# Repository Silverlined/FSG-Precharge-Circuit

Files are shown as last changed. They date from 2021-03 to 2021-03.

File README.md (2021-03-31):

# 600V Pre-charge Circuit

One of the challenges that arise in tractive systems
of electric cars is establishing a reliable connection between
the accumulator and inverter. The presented pre-charge control
circuit is a potential solution that can be used to operate a DC
contractor and prevent the flow of high inrush current into the
inverter. The circuit has been simulated in LTspice and tested
in real life across the temperature range of +10 °C to +65 °C.
Pre-charging is stopped once the inverter voltage exceeds 98%
of the voltage level of the accumulator and resumed when it is
below 95%. Regardless, this design is incomplete. There are several design flaws that have been discovered and therefore require further development.

2-layer PCB designed in EasyEDA. Gerber and assembly files are in the relevant repo folders.

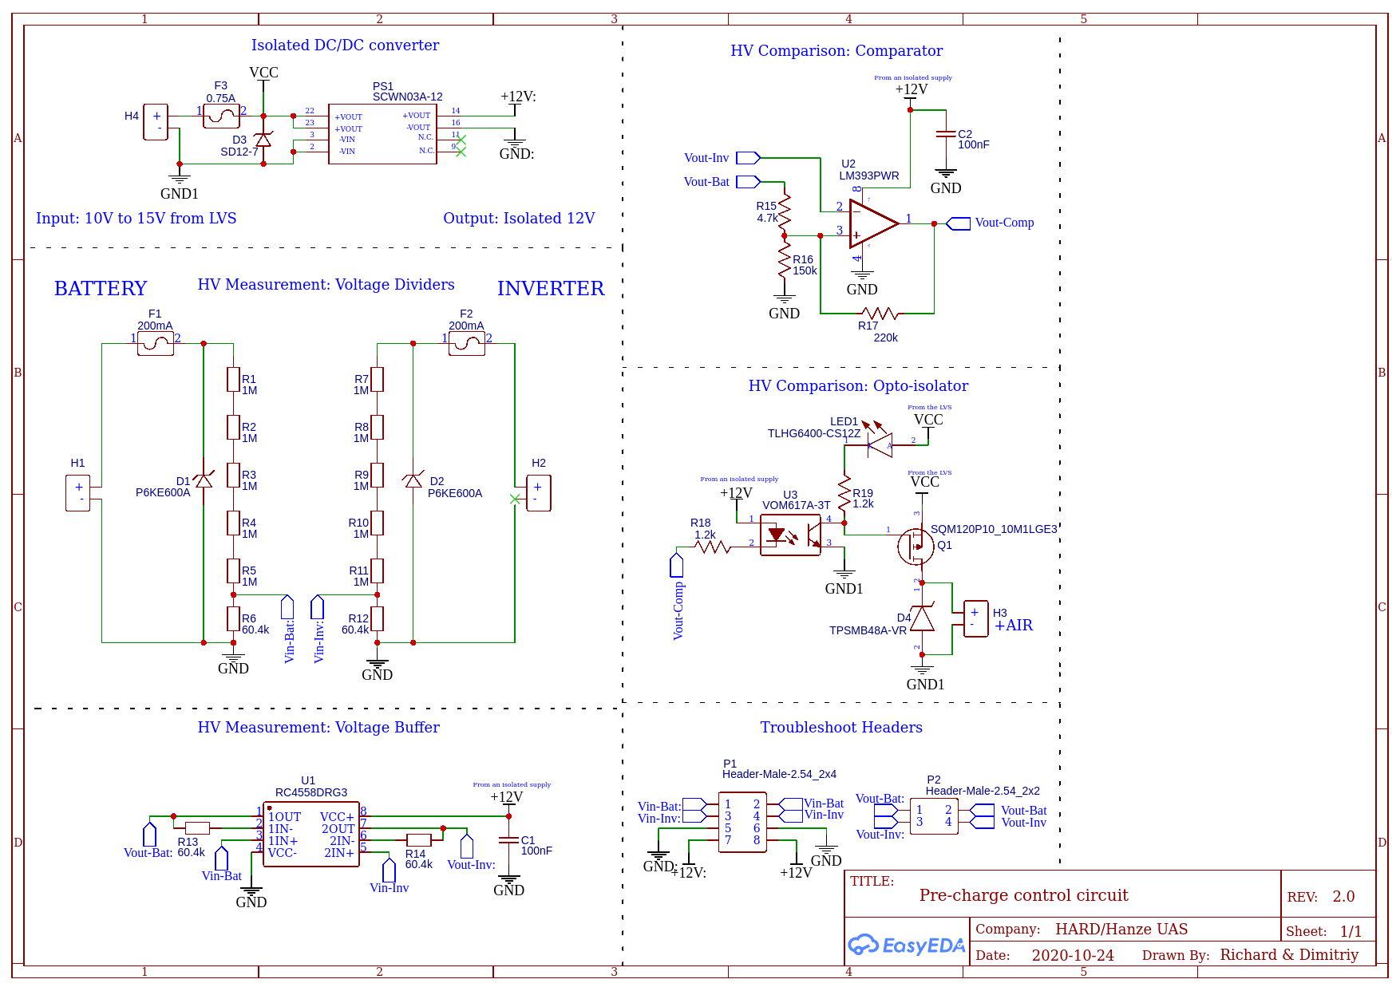
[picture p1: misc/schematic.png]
  

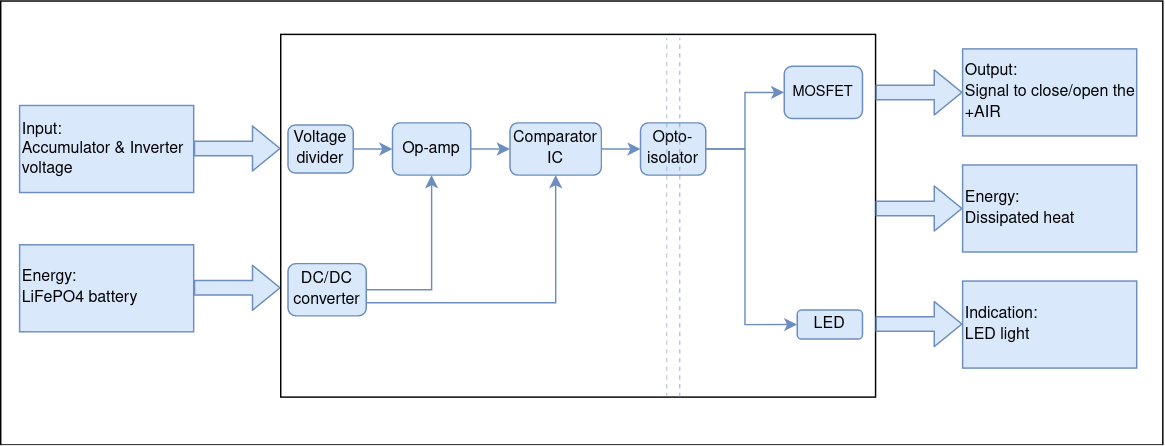
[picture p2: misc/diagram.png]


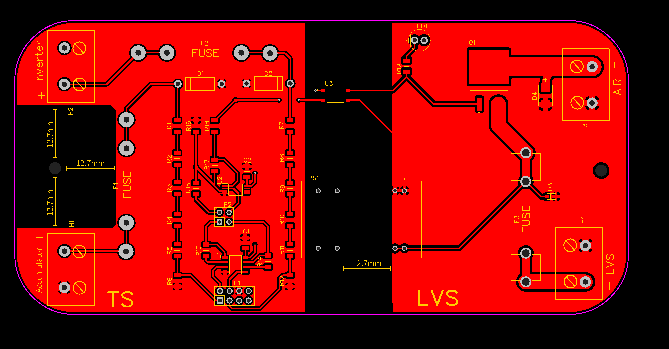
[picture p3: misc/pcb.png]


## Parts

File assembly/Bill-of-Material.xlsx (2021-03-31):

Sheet: Sheet1
Reference Designator | Part Description | Manufacturer | MPN | LTSpice Model | Quantity | Price (€) | Sub-Total (€) | Notes
Measuring
U1 | Dual Op-amp for Automotive Applications | Texas Instruments | LM2904BQDRQ1 (https://nl.mouser.com/ProductDetail/Texas-Instruments/LM2904BQDRQ1) | Download (http://www.ti.com/litv/zip/slom472a) | 1 | 0.37 | 0.37
U1 | Dual General Purpose Op-amp | Texas Instruments | RC4558D (https://nl.mouser.com/ProductDetail/Texas-Instruments/RC4558D?qs=fvkeCqCHl3A1nZVdQC3xwQ%3D%3D) | Download (http://www.ti.com/litv/zip/sloj053) | 1 | 0.31 | 0.31
C1, C2 | Decoupling capacitors for supply lines, 0.1uF, 50V, 1206 | AVX | 12065C104KAT2A (https://nl.mouser.com/ProductDetail/AVX/12065C104KAT2A?qs=WcAEtQi8OAaNkVk1OXh0eQ%3D%3D) |  | 2 | 0.22 | 0.44
R1-R5, R7-R11 | Thin Film Resistors - SMD 1MOhm, 0.1%, 250mW, 200V, 1206 | KOA Speer | RN73R2BTTD1004B25 (https://eu.mouser.com/ProductDetail/KOA-Speer/RN73R2BTTD1004B25?qs=2WXlatMagcHteT5kLiJeJA%3D%3D) |  | 10 | 0.654 | 6.54
R6, R12, R13, R14 | Thin Film Resistors - SMD 60.4KOhm, 0.1%, 250mW, 200V, 1206 | Yaego | RT1206BRD0760K4L (https://eu.mouser.com/ProductDetail/Yageo/RT1206BRD0760K4L?qs=yNCrj0CQcyLHtwaZTxJ8RQ%3D%3D) |  | 4 | 0.483 | 1.93
PS1 | Isolated 3kV DC/DC Converters 9-18Vin 12Vout 250mA 3W | MEAN WELL | SCWN03A-12 (https://nl.mouser.com/ProductDetail/MEAN-WELL/SCWN03A-12?qs=5aG0NVq1C4xiM5EN1EnuuQ%3D%3D) |  | 1 | 7.34 | 7.34
H1-H4 | Fixed Terminal Blocks 2P 9.52mm 90deg | Phoenix Contact | 1714971 (https://www.mouser.com/ProductDetail/Phoenix-Contact/1714971?qs=cyzODkzcbwDjA%252BSs8M2BCQ%3D%3D) |  | 4 | 1.71 | 6.84
Comparing
R15 | Thin Film Resistor - SMD 4.7kOhms, 0.1%, 250mW, 150V, 1206 | Vishay | TNPW12064K70BEEA (https://eu.mouser.com/ProductDetail/Vishay-Dale/TNPW12064K70BEEA?qs=2reG4Y%252BdyC8PHCI0o8bhsQ%3D%3D) |  | 1 | 0.61 | 0.61
R16 | Thin Film Resistor - SMD 150kOhm, 0.1%, 250mW, 150V, 1206 | Panasonic | ERA-8AEB154V (https://eu.mouser.com/ProductDetail/Panasonic/ERA-8AEB154V?qs=Ojoo2rCVP9SH83xv5Vt5Mw%3D%3D) |  | 1 | 0.6 | 0.6
R17 | Thin Film Resistor - SMD 220kOhm, 1%, 250mW, 150V, 1206 | KOA Speer | RN73H2BTTD2203F100 (https://eu.mouser.com/ProductDetail/KOA-Speer/RN73H2BTTD2203F100?qs=egkD4cx1ihSMUVoNjawNHg%3D%3D) |  | 1 | 0.443 | 0.443
U2 | Analog Dual Comparator, 2 to 30V supply, 5mV offset | Texas Instruments | LM393PWR (https://nl.mouser.com/ProductDetail/Texas-Instruments/LM393PWR?qs=0OT4q4QBUTLavVIrmKi4iQ%3D%3D) | Download (http://www.ti.com/litv/zip/slcj016) | 1 | 0.3 | 0.3
U3 | Transistor Output Optocoupler | Vishay | VOM617A-3T (https://nl.mouser.com/ProductDetail/Vishay-Semiconductors/VOM617A-3T?qs=e%2F7vlcXyL81zPeC5noOBQg%3D%3D) |  | 1 | 0.51 | 0.51
R18, R19 | Thick Film Resistor - SMD 1206 1/4Watt 1.21Kohms 1% - OPTO I/O, LED | Vishay/Dale | CRCW12061K21FKEAC (https://nl.mouser.com/ProductDetail/Vishay-Dale/CRCW12061K21FKEAC) |  | 2 | 0.09 | 0.18
 | ~~Thick Film Resistors - SMD 1206 4.02Kohms 1% - OPTO OUTPUT~~ | ~~Panasonic~~ | ~~ERJ-8ENF4021V~~ (https://nl.mouser.com/ProductDetail/Panasonic/ERJ-8ENF4021V?qs=8%252BG0TiN%2FgVqLzNyFhscA4A%3D%3D) |  | ~~1~~ | ~~0.093~~ |  | Replaced with 1.2k, R19 on schematic
LED1 | Green LED - THT 10mcd; 5mm 562-575nm; 2.4V Typ | Vishay | TLHG6400-CS12Z (https://nl.mouser.com/ProductDetail/Vishay-Semiconductors/TLHG6400-CS12Z?qs=nQ9vpdMXC6ABOdaEdoPV%252BA%3D%3D) |  | 1 | 0.37 | 0.37 | New LED for state indication
Q1 | MOSFET P Ch Vds -100 Vgs 20 Rds 0.015 | Vishay/Siliconix | SQM100P10-19L_GE3 (https://nl.mouser.com/ProductDetail/Vishay-Siliconix/SQM100P10-19L_GE3?qs=Vcr9%2FL0R50g336jYRCVL3A%3D%3D) |  | 1 | 2.29 | 2.29
 | MOSFET P Ch Vds -65V, Rds 0.01 | IXYS | IXTA120P065T (https://nl.mouser.com/ProductDetail/IXYS/IXTA120P065T?qs=cvHLLyFtoE3XZQ09imn6oQ%3D%3D) |  | 1 | 3.92
 | P-channel MOSFET | Vishay Semiconductors | SQM120P10_10M1LGE3 (https://nl.mouser.com/ProductDetail/Vishay-Semiconductors/SQM120P10_10M1LGE3) |  | 1 | 2.63 |  | Will be in stock again on 30/11
Circuit protection
D1, D2 | TVS Diode 600W 600V, Accumulator/Inverter Connector | Littlefuse | P6KE600A-B (https://eu.mouser.com/ProductDetail/Littelfuse/P6KE600A-B?qs=J7VcZjJ3Z9f8jTnlw0bMSQ%3D%3D) |  | 2 | 0.64 | 1.28
D3 | TVS Diode 350W 12V, DC/DC converter | Diodes Incorporated | SD12-7 (https://nl.mouser.com/ProductDetail/Diodes-Incorporated/SD12-7?qs=dbuNSGnowt3%2FTzELhSdHmA%3D%3D) |  | 1 | 0.32 | 0.32
D4 | TVS Diode 600W, 58.9V, 77.4V, AIR Connector | Littlefuse | TPSMB48A-VR (https://nl.mouser.com/ProductDetail/Littelfuse/TPSMB48A-VR?qs=AQlKX63v8RvBdQHfMjXsVg%3D%3D) |  | 1 | 0.4 | 0.4 | New, TVS diode for Q1
F1, F2 | Fuse Ceramic Tube 0.2A 600VDC max.10kA | Bel Fuse | 0ADAC0200-BE (https://eu.mouser.com/ProductDetail/Bel-Fuse/0ADAC0200-BE?qs=rrS6PyfT74eFVqji%252BsifXw%3D%3D) |  | 2 | 2.84 | 5.68
F3 | Fuse Ceramic Tube 0.75A 125VDC max.10kA, DC/DC converter | Littlefuse | 0314.750MXP (https://www.mouser.com/ProductDetail/Littelfuse/0314750MXP?qs=OJFHm2hVE4Ep2cUj3PN4Nw%3D%3D) |  | 1 | 0.97 | 0.97 | New Fuse for PS1
 | Automotive Fuse ATOF 32V 1A Low-Current Nylon | Littlefuse | 0287001.PXCN (https://nl.mouser.com/ProductDetail/Littelfuse/0287001PXCN?qs=sGAEpiMZZMsIz3CjQ1xegdbeLroawJnw6797b2Tk9hk%3D) |  | 1 | 0.23
F1, F2 | Fuse Clip 1/4" 600V 32A | Schurter | 8040.0001 (https://nl.mouser.com/ProductDetail/Schurter/80400001) |  | 4 | 0.79 | 3.16
F3 | Fuse Clip 1/4" 250V 15A | Littlefuse | 01020071Z (https://www.mouser.com/ProductDetail/Littelfuse/01020071Z?qs=hgmQaE9nnAzCBYDQcIezzw%3D%3D) |  | 2 | 0.21 | 0.42 | New Clips for F3
 | Fuse Clip ATO 500V 30A | Keystone Electronics | 3522 (https://nl.mouser.com/ProductDetail/Keystone-Electronics/3522?qs=qOqV1E1P08RWUeWQU3K7Eg%3D%3D) |  | 4 | 0.19
 |  |  |  |  |  | Total (€) | 41.305

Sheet: Sheet2
Reference Designator | Part Description | Manufacturer | MPN | Quantity | Price (€) | Sub-Total (€)
 | Measuring
U1 | Dual Op-amp for Automotive Applications | Texas Instruments | LM2904BQDRQ1 (https://nl.mouser.com/ProductDetail/Texas-Instruments/LM2904BQDRQ1) | 2 | 0.37 | 0.74
U1 | Dual General Purpose Op-amp | Texas Instruments | RC4558D (https://nl.mouser.com/ProductDetail/Texas-Instruments/RC4558D?qs=fvkeCqCHl3A1nZVdQC3xwQ%3D%3D) | 2 | 0.31 | 0.62
C1, C2 | Decoupling capacitors for supply lines, 0.1uF, 50V, 1206 | AVX | 12065C104KAT2A (https://nl.mouser.com/ProductDetail/AVX/12065C104KAT2A?qs=WcAEtQi8OAaNkVk1OXh0eQ%3D%3D) | 4 | 0.22 | 0.88
R1-R5, R7-R11 | Thin Film Resistors - SMD 1MOhm, 0.1%, 250mW, 200V, 1206 | KOA Speer | RN73R2BTTD1004B25 (https://eu.mouser.com/ProductDetail/KOA-Speer/RN73R2BTTD1004B25?qs=2WXlatMagcHteT5kLiJeJA%3D%3D) | 20 | 0.464 | 9.28
R6, R12, R13, R14 | Thin Film Resistors - SMD 60.4KOhm, 0.1%, 250mW, 200V, 1206 | Yaego | RT1206BRD0760K4L (https://eu.mouser.com/ProductDetail/Yageo/RT1206BRD0760K4L?qs=yNCrj0CQcyLHtwaZTxJ8RQ%3D%3D) | 10 | 0.266 | 2.66
PS1 | Isolated 3kV DC/DC Converters 9-18Vin 12Vout 250mA 3W | MEAN WELL | SCWN03A-12 (https://nl.mouser.com/ProductDetail/MEAN-WELL/SCWN03A-12?qs=5aG0NVq1C4xiM5EN1EnuuQ%3D%3D) | 2 | 7.34 | 14.68
H1-H4 | Fixed Terminal Blocks 2P 9.52mm 90deg | Phoenix Contact | 1714971 (https://www.mouser.com/ProductDetail/Phoenix-Contact/1714971?qs=cyzODkzcbwDjA%252BSs8M2BCQ%3D%3D) | 8 | 1.45 | 11.6
 | Comparing
R15 | Thin Film Resistor - SMD 4.7kOhms, 0.1%, 250mW, 150V, 1206 | Vishay | TNPW12064K70BEEA (https://eu.mouser.com/ProductDetail/Vishay-Dale/TNPW12064K70BEEA?qs=2reG4Y%252BdyC8PHCI0o8bhsQ%3D%3D) | 2 | 0.61 | 1.22
R16 | Thin Film Resistor - SMD 150kOhm, 0.1%, 250mW, 150V, 1206 | Panasonic | ERA-8AEB154V (https://eu.mouser.com/ProductDetail/Panasonic/ERA-8AEB154V?qs=Ojoo2rCVP9SH83xv5Vt5Mw%3D%3D) | 2 | 0.6 | 1.2
R17 | Thin Film Resistor - SMD 220kOhm, 1%, 250mW, 150V, 1206 | KOA Speer | RN73H2BTTD2203F100 (https://eu.mouser.com/ProductDetail/KOA-Speer/RN73H2BTTD2203F100?qs=egkD4cx1ihSMUVoNjawNHg%3D%3D) | 2 | 0.443 | 0.886
U2 | Analog Dual Comparator, 2 to 30V supply, 5mV offset | Texas Instruments | LM393PWR (https://nl.mouser.com/ProductDetail/Texas-Instruments/LM393PWR?qs=0OT4q4QBUTLavVIrmKi4iQ%3D%3D) | 4 | 0.3 | 1.2
U3 | Transistor Output Optocoupler | Vishay | VOM617A-3T (https://nl.mouser.com/ProductDetail/Vishay-Semiconductors/VOM617A-3T?qs=e%2F7vlcXyL81zPeC5noOBQg%3D%3D) | 2 | 0.51 | 1.02
R18, R19 | Thick Film Resistor - SMD 1206 1/4Watt 1.21Kohms 1% - OPTO I/O, LED | Vishay/Dale | CRCW12061K21FKEAC (https://nl.mouser.com/ProductDetail/Vishay-Dale/CRCW12061K21FKEAC) | 4 | 0.09 | 0.36
LED1 | Green LED - THT 10mcd; 5mm 562-575nm; 2.4V Typ | Vishay | TLHG6400-CS12Z (https://nl.mouser.com/ProductDetail/Vishay-Semiconductors/TLHG6400-CS12Z?qs=nQ9vpdMXC6ABOdaEdoPV%252BA%3D%3D) | 2 | 0.37 | 0.74
Q1 | MOSFET P Ch Vds -100 Vgs 20 Rds 0.015 | Vishay/Siliconix | SQM100P10-19L_GE3 (https://nl.mouser.com/ProductDetail/Vishay-Siliconix/SQM100P10-19L_GE3?qs=Vcr9%2FL0R50g336jYRCVL3A%3D%3D) | 2 | 2.29 | 4.58
 | Circuit protection
D1, D2 | TVS Diode 600W 600V, Accumulator/Inverter Connector | Littlefuse | P6KE600A-B (https://eu.mouser.com/ProductDetail/Littelfuse/P6KE600A-B?qs=J7VcZjJ3Z9f8jTnlw0bMSQ%3D%3D) | 4 | 0.64 | 2.56
D3 | TVS Diode 350W 12V, DC/DC converter | Diodes Incorporated | SD12-7 (https://nl.mouser.com/ProductDetail/Diodes-Incorporated/SD12-7?qs=dbuNSGnowt3%2FTzELhSdHmA%3D%3D) | 2 | 0.32 | 0.64
D4 | TVS Diode 600W, 58.9V, 77.4V, AIR Connector | Littlefuse | TPSMB48A-VR (https://nl.mouser.com/ProductDetail/Littelfuse/TPSMB48A-VR?qs=AQlKX63v8RvBdQHfMjXsVg%3D%3D) | 2 | 0.4 | 0.8
F1, F2 | Fuse Ceramic Tube 0.2A 600VDC max.10kA | Bel Fuse | 0ADAC0200-BE (https://eu.mouser.com/ProductDetail/Bel-Fuse/0ADAC0200-BE?qs=rrS6PyfT74eFVqji%252BsifXw%3D%3D) | 4 | 2.84 | 11.36
F3 | Fuse Ceramic Tube 0.75A 125VDC max.10kA, DC/DC converter | Littlefuse | 0314.750MXP (https://www.mouser.com/ProductDetail/Littelfuse/0314750MXP?qs=OJFHm2hVE4Ep2cUj3PN4Nw%3D%3D) | 2 | 0.97 | 1.94
F1, F2 | Fuse Clip 1/4" 600V 32A | Schurter | 8040.0001 (https://nl.mouser.com/ProductDetail/Schurter/80400001) | 8 | 0.79 | 6.32
F3 | Fuse Clip 1/4" 250V 15A | Littlefuse | 01020071Z (https://www.mouser.com/ProductDetail/Littelfuse/01020071Z?qs=hgmQaE9nnAzCBYDQcIezzw%3D%3D) | 4 | 0.21 | 0.84
 | Extra, Testing
 | 555 Type, Timer/Oscillator IC 1MHz 8-PDIP | Renesas | ICM7555IPAZ (https://eu.mouser.com/ProductDetail/Renesas-Intersil/ICM7555IPAZ?qs=9fLuogzTs8J%2FHpiW%2F2tlyQ%3D%3D) | 3 | 0.7 | 2.1
 | Slide Switch SPDT Through Hole | E-Switch | EG1218 (https://eu.mouser.com/ProductDetail/E-Switch/EG1218?qs=xDsBkp9LkocT0c8K%252B5e%2FgA%3D%3D) | 3 | 0.5 | 1.5
 | 100µF 16V Aluminum Electrolytic Capacitor 5x2mm | Rubycon | 16ZLH100MEFC5X11 (https://eu.mouser.com/ProductDetail/Rubycon/16ZLH100MEFC5X11) | 3 | 0.2 | 0.6
 | 10µF 16V Aluminum Electrolytic Capacitor 4x1.5mm | Nichicon | USA1C100MDD1TP (https://eu.mouser.com/ProductDetail/Nichicon/USA1C100MDD1TP) | 3 | 0.14 | 0.42
 | Battery Holder 2032 Coin Cell | Keystone Electronics | 1066 (https://nl.mouser.com/ProductDetail/Keystone-Electronics/1066?qs=TMDrOSIpnUfyx7dWA5t7YA%3D%3D) | 3 | 1.26 | 3.78
 | Red 3mm LED - Discrete 1.85V | Lumex | SSL-LX3054SRD (https://eu.mouser.com/ProductDetail/Lumex/SSL-LX3054SRD?qs=vbU4ZYfMnUqs%252BFBcC%2F2AyA%3D%3D) | 10 | 0.212 | 2.12
 | BJT NPN 40V 200MA TO92-3 | ON Semiconductor | 2N3904BU (https://eu.mouser.com/ProductDetail/ON-Semiconductor-Fairchild/2N3904BU?qs=or4AE2qAS%252Bd0Jdpn%2F8ktKg%3D%3D) | 3 | 0.17 | 0.51
 |  |  |  |  | Total (€) | 87.156

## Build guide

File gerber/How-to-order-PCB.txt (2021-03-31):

How to Order PCB

Please refer to:
https://docs.easyeda.com/en/PCB/Order-PCB

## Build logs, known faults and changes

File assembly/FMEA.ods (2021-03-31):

(Failure Mode and Effect Analysis) FMEA |  |  |  |  |  |  |  |  |  | O | Occurrence | Failure Rate (1/MTTF)
Sub-block |  | Failure mode | Causes of failure | Effects of failure | Rating |  |  |  | Action status | 1 | 20 to 30+ years
Nr | System, part, component |  |  |  | O | S | D | RPN | Recommended actions | 2 | 10 to 20 years
1 | Accumulator isolation relay (AIR) | 1.1 Failure to Trip | Degradation failure – mechanical wear, high-sustained current, voltage spikes. | Failure to close the relay will results in an open circuit between the accumulator and the inverter, therefore there will be no power to drive the car. | 3 | 3 | 1 | 9 | Replace in case of failure. | 3 | 1 to 10 years
 |  | 1.2 Spurious Trip | Degradation failure – mechanical wear, high-sustained current, voltage spikes. | Failure to close the relay will results in an open circuit between the accumulator and the inverter, therefore there will be no power to drive the car. | 3 | 3 | 1 | 9 | Replace in case of failure. | 4 | 0 to 1 year
 |  | 1.3 Short/Welded contacts | Random failure – contamination of the contacts, high in-rush current. | Failure to open the relay will results in an unwanted closed circuit between the accumulator and the inverter. The safety management system will be triggered. | 2 | 4 | 1 | 8 | Soft starting circuit is required to prevent in-rush currents. Detectable by continuity check. Replace in case of failure.
2 | Thin Film Resistors | 2.1 Open circuit | Random failure – handling damage, ESD, external stress, overload. | Measurement and comparison of the voltage levels of the accumulator and the inverter will not be achievable. The control circuit for the AIR will not work. | 2 | 3 | 1 | 6 | Be careful when handling the components, wear anti-static bracelet. Detectable by continuity check. Replace in case of failure. | S | Severity
 |  | 2.2 Resistance drift | Degradation failure/Random failure – handling damage, ESD, external stress, overload. | Changes in the resistance values will result in voltage drift in design specifications. | 3 | 1 | 2 | 6 | Be careful when handling the components, wear anti-static bracelet. No special actions warranted. | 1 | No Effect
 |  | 2.3 Short circuit | Random failure – handling damage, ESD, external stress, overload. | Exceeding upper or lower voltage specification limits. | 1 | 3 | 1 | 3 | Be careful when handling the components, wear anti-static bracelet. Detectable by continuity check. Replace in case of failure. | 2 | Maintenance
 |  |  |  |  |  |  |  |  |  | 3 | Replacement
3 | Operational Amplifier | 3.1 Short circuit | Random failure – handling damage, ESD, external stress, overload. | Internal short will cause the buffering amplifier to send out wrong or no signal to the comparator. | 2 | 3 | 1 | 6 | Detectable by continuity check. Replace in case of failure. | 4 | Blind Failure
 |  | 3.2 Parameter change | Degradation failure/Random failure – handling damage, ESD, external stress, overload. | Changes in the input bias voltage will cause wrong measurements to be buffered and sent out to the comparator. | 3 | 3 | 2 | 18 | Replace in case of failure.
 |  | 3.3 Feedback resistor – open | Random failure – handling damage, ESD, external stress, overload. | Open connection in the feedback path will prevent negative feedback which will result in saturated output signal to the power rails. | 2 | 2 | 1 | 4 | No special actions warranted. Replace resistor. | D | Detectability
 |  | 3.4 Decoupling capacitor – short | Random failure – handling damage, ESD, external stress, overload. | The positive terminal of the DC/DC converter will be shorted to ground and the protective fuse will be triggered. The circuit will have no power. | 1 | 2 | 1 | 2 | No special actions warranted. Replace capacitor. | 1 | Detectable
 |  |  |  |  |  |  |  |  |  | 2 | Non-detectable
4 | Comparator | 4.1 Short circuit | Random failure – handling damage, ESD, external stress, overload. | Internal short will cause the comparator to send out wrong or no signal to the optocoupler. | 2 | 3 | 1 | 6 | Detectable by continuity check. Replace in case of failure.
 |  | 4.2 Parameter change | Degradation failure/Random failure – handling damage, ESD, external stress, overload. | Changes in the input bias voltage will cause changes in the comparison threshold levels which may result in sending out wrong signal to the optocoupler. | 3 | 1 | 2 | 6 | No special actions warranted.
 |  | 4.3 Feedback resistor – open | Random failure – handling damage, ESD, external stress, overload. | Open connection in the feedback path will cease the created hysteresis which may result in sending out wrong signal to the optocoupler. | 2 | 2 | 1 | 4 | No special actions warranted. Replace resistor.
 |  | 4.1 Decoupling capacitor – short | Random failure – handling damage, ESD, external stress, overload. | The positive terminal of the DC/DC converter will be shorted to ground and the protective fuse will be triggered. The circuit will have no power. | 1 | 2 | 1 | 2 | No special actions warranted. Replace capacitor.
5 | Optocoupler | 5.1 Short circuit | Random failure – handling damage, ESD, external stress, overload. | Internal short will cause the optocoupler to send out wrong or no signal to the MOSFET. | 2 | 3 | 1 | 6 | Detectable by continuity check. Replace in case of failure.
 |  | 5.2 Transistor output failure | Degradation failure – high-sustained current, voltage spikes Random failure – handling damage, ESD, external stress, overload. | Failure to trigger the transistor output will result in sending out no signal to the MOSFET. | 3 | 3 | 2 | 18 | Replace in case of failure.
6 | MOSFET | 6.1 Avalanche failure | Degradation failure - maximum operating voltage of the MOSFET is exceeded, high back EMF. | Avalanche breakdown may not necessarily be destructive to the to MOSFET. However, exceeding the specification limit may result in faulty operation. | 3 | 3 | 1 | 9 | Replace in case of failure.
 |  | 6.2 Gate breakdown | Random failure – voltage spikes, in-rush current. | Gate-body insulation of the MOSFET is destroyed It becomes non-functional. The AIR will not be controlled. | 3 | 4 | 1 | 12 | Replace in case of failure.
 | O = Occurrence of failure
 | S = Severity of failure
 | D = Detectability of failure
 | RPN (=O*S*D)
